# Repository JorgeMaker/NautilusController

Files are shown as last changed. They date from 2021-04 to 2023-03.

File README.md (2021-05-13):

<p align="center">
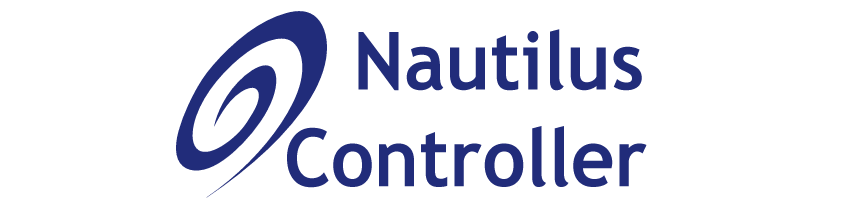
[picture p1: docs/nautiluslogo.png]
  
</p>

## *Nautilus Brushless Controller*

The Nautilus Controller, a project still under development will to turn a hobby brushless motors into a robotic servo actuator  for precise control of 3-phase brushless motors.

The board  integrates the necessary drive electronics, a high performance SMT32 microcontroller, an absolute magnetic encoder, and a high-speed data interface in a compact board that cab be attached at the rear part of a BLDC motor.

<p align="center">
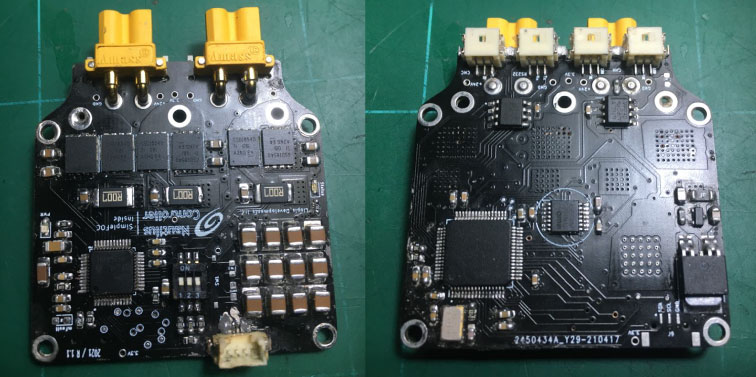
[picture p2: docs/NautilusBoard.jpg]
  
</p>

Some features of the project under development are:

- Compact size of 48x48 mm 4-layer PCB
- SMT32F405RGT6 as MCU
- Uses the DRV8305 as gate driver.
- Absolute 14 bits magnetic encoder AS5048A with SPI communications
- Power Connector: 2x XT30PW-F
- Dual connector of CAN bus interface
- Data Connector: 4x Hirose DF13
- Status LEDs
- RS232 communications
- Temperature sensor

It will be able to operate in in torque, velocity or position modes, using Field Oriented Control (FOC) developed using the open source project [SimpleFOC](https://github.com/simplefoc). For communications it will offer a dual interface based on CAN bus (not implemented yet) for a reliable network communication and RS322 for configuration and basic operation.

The ultimate goal of the controller under development is to be able to develop A ROS actuator that can be used to build dynamic robots like, as for examples, a robot arm or a quadruped robot.

As previously stated, this project is still in the very early stages of development, under construction and continuous change so take it in consideration if you decide to reuse some of the provided information.

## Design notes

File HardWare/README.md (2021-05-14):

### Nautilus Controller Hardware

In this folder you can find the schematic in pdf format to reproduce in your desired EDA software tool. Gerber files are provided too in order to guide you how to layout the components. Since we are in a middle of a global semiconductors shortage BOM is not provided since most probably some of the components used will not be available ;(

<p align="center">
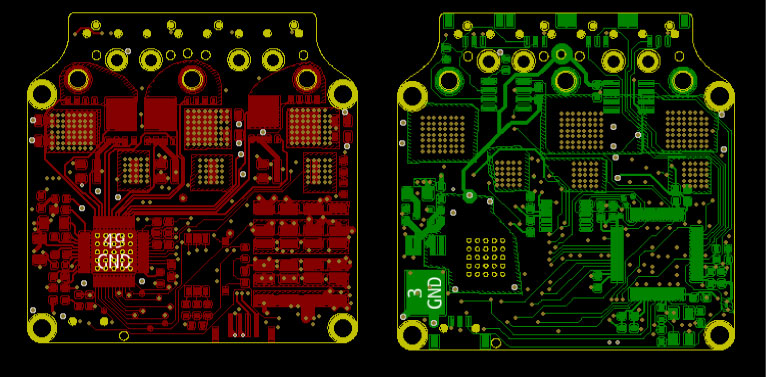
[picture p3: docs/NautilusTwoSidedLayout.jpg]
  
</p>

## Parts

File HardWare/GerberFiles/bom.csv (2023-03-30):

Designator | Footprint | Quantity | Value | LCSC Part #
C1 | 0603 | 1 | 100nF
C10 | 0603 | 1 | 2.2µF
C11 | 0603 | 1 | 15pF
C12 | 0603 | 1 | 15pF
C13 | 1206 | 1 | 4.7μF
C14 | 0603 | 1 | 1µF
C15 | 0603 | 1 | 1µF
C16 | 0603 | 1 | 47nF
C17 | 0603 | 1 | 47nF
C18 | 1206 | 1 | 2.2µF
C19 | 0603 | 1 | 1µF
C2 | 0603 | 1 | 100nF
C20 | 0603 | 1 | 10µF
C21 | 0603 | 1 | 10µF
C22 | 0603 | 1 | 100nF
C23 | 0603 | 1 | 1µF
C24 | 0603 | 1 | 100nF
C25 | 0603 | 1 | 100nF
C26 | 0603 | 1 | 10µF
C27 | 0603 | 1 | 1nF
C28 | 0603 | 1 | 1nF
C29 | 0603 | 1 | 1nF
C3 | 0603 | 1 | 100nF
C30 | 0805 | 1 | 1µF
C31 | 0805 | 1 | 1µF
C32 | 0805 | 1 | 1µF
C33 | 0805 | 1 | 10µF
C34 | 0805 | 1 | 10µF
C35 | 0805 | 1 | 10µF
C36 | 0805 | 1 | 10µF
C37 | 0805 | 1 | 10µF
C38 | 0805 | 1 | 10µF
C39 | 1210 | 1 | 10µF
C4 | 0603 | 1 | 100nF
C40 | 1210 | 1 | 10µF
C41 | 1210 | 1 | 10µF
C42 | 1210 | 1 | 10µF
C43 | 1210 | 1 | 10µF
C44 | 1210 | 1 | 10µF
C45 | 1210 | 1 | 10µF
C46 | 1210 | 1 | 10µF
C47 | 1210 | 1 | 10µF
C48 | 1210 | 1 | 10µF
C49 | 1210 | 1 | 10µF
C5 | 0603 | 1 | 100nF
C50 | 1210 | 1 | 10µF
C51 | 0603 | 1 | 100nF
C52 | 0603 | 1 | 100nF
C6 | 0603 | 1 | 100nF
C7 | 0603 | 1 | 1µF
C8 | 0603 | 1 | 4.7µF
C9 | 0603 | 1 | 2.2µF
D1 | 0603 | 1 | Red
D2 | 0603 | 1 | Green
D3 | 0603 | 1 | Blue
D4 | LED_WS2812B-2020_PLCC4_2.0x2.0mm | 1 | WS2812B
F1 | 1206 | 1 | 500mA | C841189
FB1 | 0603 | 1 | 330Ω @ 100MHz | C35327
H1 | MountingHole_2.5mm_Pad | 1 | H1
H2 | MountingHole_2.5mm_Pad | 1 | H2
H3 | MountingHole_2.5mm_Pad | 1 | H3
H4 | MountingHole_2.5mm_Pad | 1 | H4
HSE1 | TAXM8M4RDBCCT2T | 1 | 8Mhz | C400090
J1 | XT30PW-M | 1 | Power Conn A
J10, J20 | PowerPad | 2 | Rx
J11 | PowerPad | 1 | H
J12 | PowerPad | 1 | SCL
J13, J21 | PowerPad | 2 | Tx
J14 | PowerPad | 1 | L
J15, J9 | PowerPad | 2 | SDA
J16 | JST1.25_3PH | 1 | Comm Conn A
J17 | JST1.25_3PH | 1 | RS232 Conn
J18 | JST1.25_3PH | 1 | Conn Comn B
J19 | PowerPad | 1 | CRTL
J2 | PowerPad | 1 | DIR PAD
J3 | PowerPad | 1 | STEP PAD
J4 | XT30PW-M | 1 | Power Conn B
J5 | SolderRescue | 1 | LOOP PIN
J6 | PinHeader_1x04_P2.00mm_Vertical | 1 | Prog conn
J7 | SolderRescue | 1 | CAN_RX
J8 | SolderRescue | 1 | CAN_TX
Q1 | SSOT-3 | 1 | FDN352AP
Q2, Q3, Q4, Q5, Q6, Q7 | BSC022N04LS6ATMA1 | 6 | BSC022N04LS
R1 | 0603 | 1 | 1KΩ
R10 | 0603 | 1 | 10KΩ
R11, R12, R13 | CurrentSense | 3 | 2mΩ
R14 | 0603 | 1 | 10KΩ
R15 | 0603 | 1 | 120Ω
R16 | 0603 | 1 | 10KΩ
R2 | 0603 | 1 | 10KΩ
R3 | 0603 | 1 | 10K
R4 | 0603 | 1 | 220Ω
R5 | 0603 | 1 | 100Ω
R6 | 0603 | 1 | 10KΩ
R7 | 0603 | 1 | 20KΩ
R8 | 0603 | 1 | 2KΩ
R9 | 0603 | 1 | 10KΩ
SW1 | SimplePushButton | 1 | Reset Push
TP1 | MinimalTP | 1 | INH_A_TP
TP10, TP11 | MinimalTP | 2 | INL_C_TP
TP12 | MinimalTP | 1 | mFAULT
TP13 | MinimalTP | 1 | MOSI_ENC
TP14 | MinimalTP | 1 | MISO_ENC
TP15 | MinimalTP | 1 | CLK_ENC
TP16 | MinimalTP | 1 | CS_ENC
TP17 | MinimalTP | 1 | ENC PWM
TP18 | MinimalTP | 1 | SENSE A
TP19 | MinimalTP | 1 | SENSE C
TP2 | MinimalTP | 1 | CS
TP20 | MinimalTP | 1 | SENSE B
TP3 | MinimalTP | 1 | INL_A_TP
TP4 | MinimalTP | 1 | MOSI
TP5 | MinimalTP | 1 | INH_B_TP
TP6 | MinimalTP | 1 | MISO
TP7 | MinimalTP | 1 | INL_B_TP
TP8 | MinimalTP | 1 | CLK
TP9 | MinimalTP | 1 | INH_C_TP
U1 | TO114P998X235-5 | 1 | BD33C0AWFP
U10, U12, U8, U9 | PowerPad | 4 | Power24VPad
U11 | PowerPad | 1 | PowerPad I2C
U13 | MinimalPhasePad | 1 | PhaseA
U14 | MinimalPhasePad | 1 | PhaseB
U15 | MinimalPhasePad | 1 | PhaseC
U2 | LQFP-64_10x10mm_P0.5mm | 1 | STM32F405RGT6
U3 | QFP50P900X900X120-49N | 1 | DRV8305 | LCSC Part #
U4 | SOP-8_3.9x4.9mm_P1.27mm | 1 | LM75B
U5 | SOIC-8_3.9x4.9mm_P1.27mm | 1 | SN65HVD231 | C12084
U6 | TSSOP-14_4.4x5mm_P0.65mm | 1 | AS5048A | C2655181
U7 | MiniLogo | 1 | Logo

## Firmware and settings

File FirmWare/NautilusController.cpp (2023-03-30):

#include <SimpleFOC.h>
#include "STM32F405RTGBorad.h"
#include <SimpleCanFacility.h>
#include <NautilusCANMessage.h>
#include <TrapezoidalPlanner.h>
#include <Adafruit_NeoPixel.h>
#include <TemperatureSensor.h>

///    SPI 2 (AS5048A)
#define MOSI_DRV  PA7  // Blue
#define MISO_DRV  PA6 // Green
#define CLK_DRV   PA5 // Orange
#define CS_DRV    PA4  // Yellow

///     SPI 1  (DRV8305)
#define MOSI_ENC PB15 // Blue
#define MISO_ENC PB14  // Green
#define CLK_ENC  PB13   // Orange
#define CS_ENC   PB12    // Yellow

#define INH_A PC7 // TIM8_CH2
#define INH_B PA1 // TIM2_CH2
#define INH_C PA3 // TIM2_CH4

#define INL_A PC6 // TIM8-CH1
#define INL_B PA0 // TIM2-CH1
#define INL_C PA2 // TIM2-CH3

#define ENA_GATE PC3

#define SENSE_A PB1
#define SENSE_B PB0
#define SENSE_C PC5

#define BLUE_LED PB2
#define LOOP_PIN PC13

#define RGB_PIN PB5
#define LED_COUNT  1

#define NUM_OF_BLINKS 16

void bootLedIndicator()
{
  int counter = NUM_OF_BLINKS;
  pinMode(BLUE_LED, OUTPUT);
  while (counter > 0)
  {
    digitalToggle(BLUE_LED);
    delay(50);
    counter--;
  }
}

Adafruit_NeoPixel regIndicator = Adafruit_NeoPixel(LED_COUNT, RGB_PIN, NEO_GRB + NEO_KHZ800);
bool regIndicatorStatus = false;

void initRGBIndicator(){
    regIndicator.begin();
    regIndicator.setBrightness(20);
} 
void showRGBColor(int red, int green, int blue){
    regIndicator.setPixelColor(0, regIndicator.Color(red, green, blue));
    regIndicatorStatus = true;
    regIndicator.show();
}

void setRGBColor(int red, int green, int blue){
    regIndicator.setPixelColor(0, regIndicator.Color(red, green, blue));
}

 void togggleRGB(){
    if (regIndicatorStatus){
      regIndicator.setBrightness(0);
      regIndicator.show();
    }
    else{
      regIndicator.setBrightness(15);
      regIndicator.setPixelColor(0, regIndicator.Color(255, 0, 255));
      regIndicator.show();
    }
    regIndicatorStatus = !regIndicatorStatus;
 }



SimpleCanFacility canFacility;
NautilusCANMesage nautilusMsg;
double lastTime;

SPIClass spiConnectionDRV(MOSI_DRV, MISO_DRV, CLK_DRV);

void configureAmplierClamping(SPIClass spiConnectionToDRV){
  // Clamp sense amplifier output to 3.3V
  digitalWrite(CS_DRV, LOW);
  byte resp1 = spiConnectionToDRV.transfer(B01001100);
  byte resp2 = spiConnectionToDRV.transfer(B10100000);
  digitalWrite(CS_DRV, HIGH);
  Serial.println("Configure Amplier Clamping");
  Serial.print("Byte 0 : ");
  Serial.println(resp1, BIN);
  Serial.print("Byte 1 : ");
  Serial.println(resp2, BIN);
}
void configure6PWM_Mode(SPIClass spiConnectionToDRV){
  // Set to three PWM inputs mode to 6PWM
  digitalWrite(CS_DRV, LOW);
  byte resp1 = spiConnectionToDRV.transfer(B00111010);
  byte resp2 = spiConnectionToDRV.transfer(B0000110);
  digitalWrite(CS_DRV, HIGH);
  Serial.println("Configure 6PWM Mode");
  Serial.print("Byte 0 : ");
  Serial.println(resp1, BIN);
  Serial.print("Byte 1 : ");
  Serial.println(resp2, BIN);
}

void drv8305Initialization()
{
  Serial.println("DRIVER: DRV8305 INIT");
  pinMode(ENA_GATE, OUTPUT);
  pinMode(CS_DRV, OUTPUT);
  digitalWrite(CS_DRV, HIGH);
  configure6PWM_Mode(spiConnectionDRV);
  configureAmplierClamping(spiConnectionDRV);
  _delay(500);
  Serial.println("DRIVER: enGate Enabled");
  digitalWrite(ENA_GATE, HIGH);
}

MagneticSensorSPIConfig_s AS5047A_SPI_Config{
    .spi_mode = SPI_MODE1,
    .clock_speed = 10000000,
    .bit_resolution = 14,
    .angle_register = 0x3FFF,
    .data_start_bit = 13,
    .command_rw_bit = 14,
    .command_parity_bit = 15};

MagneticSensorSPI sensor = MagneticSensorSPI(AS5047A_SPI_Config, CS_ENC);

SPIClass spiConnectionEncoder(MOSI_ENC, MISO_ENC, CLK_ENC);

// BLDC motor & driver instance
BLDCMotor motor = BLDCMotor(7);
//BLDCMotor motor = BLDCMotor(12);

// BLDCDriver3PWM driver = BLDCDriver3PWM (INH_A,INH_B, INH_C, ENA_GATE);
BLDCDriver6PWM driver = BLDCDriver6PWM(INH_A, INL_A, INH_B, INL_B, INH_C, INL_C, ENA_GATE);

LowsideCurrentSense current_sense = LowsideCurrentSense(0.007f, 12.22f, SENSE_A, SENSE_B, SENSE_C);

Commander commander = Commander(Serial);

TrapezoidalPlanner planner(10);

TemperatureSensor temperature;

void doPlanner(char *cmd){
  planner.doTrapezoidalPlannerCommand(cmd);
}

void doMotor(char *cmd){
  commander.motor(&motor, cmd);
}

void configureNuathilus(){
  // control loop type and torque mode
  motor.torque_controller = TorqueControlType::foc_current;
  motor.controller = MotionControlType::velocity_openloop;
  motor.motion_downsample = 0.0;
  driver.voltage_power_supply = 22;
  
  // velocity loop PID
  motor.PID_velocity.P = 10.0;
  motor.PID_velocity.I = 10.0;
  motor.PID_velocity.D = 0.0;
  motor.PID_velocity.output_ramp = 1000.0;
  motor.PID_velocity.limit = 20.0;
  // Low pass filtering time constant
  motor.LPF_velocity.Tf = 0.2;
  
  // angle loop PID
  motor.P_angle.P = 10.0;
  motor.P_angle.I = 1.0;
  motor.P_angle.D = 0.0;
  motor.P_angle.output_ramp = 0.0;
  motor.P_angle.limit = 10.0;
  // Low pass filtering time constant
  motor.LPF_angle.Tf = 0.3;
  
  // current q loop PID
  motor.PID_current_q.P = 3.0;
  motor.PID_current_q.I = 300.0;
  motor.PID_current_q.D = 0.0;
  motor.PID_current_q.output_ramp = 0.0;
  motor.PID_current_q.limit = 12.0;
  
  // Low pass filtering time constant
  motor.LPF_current_q.Tf = 0.005;
  
  // current d loop PID
  motor.PID_current_d.P = 3.0;
  motor.PID_current_d.I = 300.0;
  motor.PID_current_d.D = 0.0;
  motor.PID_current_d.output_ramp = 0.0;
  motor.PID_current_d.limit = 12.0;
  
  // Low pass filtering time constant
  motor.LPF_current_d.Tf = 0.005;
  
  
  // Limits
  motor.velocity_limit = 30.0;
  motor.voltage_limit = 1;

  // motor.current_limit = 2.0;

  //  general settings
  //  pwm modulation settings
  motor.foc_modulation = FOCModulationType::SinePWM;
  motor.modulation_centered = 1.0;
}

void setup(){

  bootLedIndicator();
  Serial.begin(115200);

  initRGBIndicator();
  setRGBColor(255,0,0);

  // I2C for temperature Sensor
  Wire.begin(PB7, PB6);

  Serial.println("Starting Motor configuration ....");

  canFacility.init(Kbit250, NormalCAN);
  canFacility.configSnniferFilter();
  canFacility.activateNotification();
  canFacility.begin();

  lastTime = millis();

  pinMode(LOOP_PIN, OUTPUT);

  char motor_id = 'M';
  commander.add(motor_id, doMotor, "Motor");

  motor.useMonitoring(Serial);
  pinMode(BLUE_LED, OUTPUT);
  sensor.init(&spiConnectionEncoder);

  // DRV8305 Inicialization
  spiConnectionDRV.begin();
  spiConnectionDRV.setBitOrder(MSBFIRST);
  spiConnectionDRV.setDataMode(SPI_MODE1);
  spiConnectionDRV.setClockDivider(SPI_CLOCK_DIV8);
  drv8305Initialization();


  // Configure and init Temperature Sensor
  temperature.init();

  ///   TODO TODO TODO
  ///   RESOLVE HW ISSUE
  // link the motor to the sensor
  //motor.linkSensor(&sensor);

  driver.voltage_power_supply = 22;
  driver.init();
  driver.enable();

  // link the motor and the driver
  motor.linkDriver(&driver);
  configureNuathilus();

  //  GCode move Gxx, GVxx, or GAxx - Example: G30 moves to position in rads. 
  //  GV10 sets velocity to 10 rads/s. GA5 sets acceleration to 5 rads/s/s.");
  planner.linkMotor(&motor);
  commander.add('G', doPlanner, "Motion Planner");

  motor.target = 10;
 
  Serial.println("LCS ready to be linked ...");
  current_sense.linkDriver(&driver);
  Serial.println("LCS ready just linked ...");
  current_sense.init();
  Serial.println("LCS ininitiated ...");
  // link the current sense to the motor
  motor.linkCurrentSense(&current_sense);
  Serial.println("LCS lined with motor ...");
  // skip alignment
  current_sense.skip_align = true;
  //current_sense.driverAlign();

  // initialize motor
  motor.init();
  motor.initFOC();

  Serial.println("Motor ready.");
  _delay(1000);
}

float value;

void sendTemperatureByCanBus(){
  nautilusMsg.setEncodeMessageID(ANGLE_STATE, FLOAT, 5, 0, 10);
  float temp = temperature.readTemperatureC();
  nautilusMsg.setFloatPayload(temp);
  canFacility.send(nautilusMsg.toCanMessage());
}

CanMessage rxMsgBuff[3];
int nodeID = 5;
int entity = 10;

void attendCanBusCommands(){
  int receivedMessages = canFacility.receiveCanMessages(rxMsgBuff);
  if (receivedMessages > 0){
    togggleRGB();
    //digitalToggle(BLUE_LED);
    for (int index = 0; index < receivedMessages; index++){
      NautilusCANMesage nautilusMsg = rxMsgBuff[index];
      if ((nautilusMsg.getNodeID() == nodeID) & (nautilusMsg.getEntity() == entity)){
        if (nautilusMsg.getCommandID() == TARGET_CMD){
          motor.target = nautilusMsg.getFloatPayload();
          motor.move(motor.target);
        }
      }
    }
  }
}

void loop()
{

  if ((millis() - lastTime) > 100){
    digitalToggle(BLUE_LED);
    sendTemperatureByCanBus();
    lastTime = millis();
  }
  
  motor.loopFOC();
  motor.move();
  commander.run();
  planner.runPlannerOnTick();
  motor.monitor();
  attendCanBusCommands();
  
  digitalToggle(LOOP_PIN);
}

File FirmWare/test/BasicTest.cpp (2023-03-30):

/*
#include <SimpleFOC.h>
#include "STM32F405RTGBorad.h"

///    SPI 2 (AS5048A)
#define MOSI_DRV PA7 // Blue
#define MISO_DRV PA6 // Green
#define CLK_DRV PA5  // Orange
#define CS_DRV PA4   // Yellow

///     SPI 1  (DRV8305)
#define MOSI_ENC PB15 // Blue
#define MISO_ENC PB14 // Green
#define CLK_ENC PB13  // Orange
#define CS_ENC PB12   // Yellow

#define INH_A PC7 // TIM8_CH2
#define INH_B PA1 // TIM2_CH2
#define INH_C PA3 // TIM2_CH4

#define INL_A PC6 // TIM8-CH1
#define INL_B PA0 // TIM2-CH1
#define INL_C PA2 // TIM2-CH3

#define ENA_GATE PC3
#define nMFAULT PC4  

#define BLUE_LED PB2
#define LOOP_PIN PC13

#define BLUE_LED PB2
#define LOOP_PIN PC13

#define SENSE_A PB1
#define SENSE_B PB0
#define SENSE_C PC5


#define NUM_OF_BLINKS 15

void bootLedIndicator()
{
  int counter = NUM_OF_BLINKS;
  pinMode(BLUE_LED, OUTPUT);
  while (counter > 0)
  {
    digitalToggle(BLUE_LED);
    delay(50);
    counter--;
  }
}
double lastTime;

void setOutPutMode(){

  pinMode(MOSI_DRV, OUTPUT);
  pinMode(MISO_DRV, OUTPUT);
  pinMode(CLK_DRV, OUTPUT);
  pinMode(CS_DRV, OUTPUT);

  pinMode(MOSI_ENC, OUTPUT);
  pinMode(MISO_ENC, OUTPUT);
  pinMode(CLK_ENC, OUTPUT);
  pinMode(CS_ENC, OUTPUT);

  pinMode(INH_A, OUTPUT);
  pinMode(INH_B, OUTPUT);
  pinMode(INH_C, OUTPUT);

  pinMode(INL_A, OUTPUT);
  pinMode(INL_B, OUTPUT);
  pinMode(INL_C, OUTPUT);

  pinMode(ENA_GATE, OUTPUT);
  pinMode(nMFAULT, OUTPUT);

  pinMode(SENSE_A, OUTPUT);
  pinMode(SENSE_B, OUTPUT);
  pinMode(SENSE_C, OUTPUT);

}

void togglePins(){
  digitalToggle(MOSI_DRV);
  digitalToggle(MISO_DRV);
  digitalToggle(CLK_DRV);
  digitalToggle(CS_DRV);

  digitalToggle(MOSI_ENC);
  digitalToggle(MISO_ENC);
  digitalToggle(CLK_ENC);
  digitalToggle(CS_ENC);

  digitalToggle(INH_A);
  digitalToggle(INH_B);
  digitalToggle(INH_C);

  digitalToggle(INL_A);
  digitalToggle(INL_B);
  digitalToggle(INL_C);

  digitalToggle(ENA_GATE);
  digitalToggle(nMFAULT);

  digitalToggle(SENSE_A);
  digitalToggle(SENSE_B);
  digitalToggle(SENSE_C);

}

void setup()
{
  Serial.begin(115200);
  pinMode(BLUE_LED, OUTPUT);
  pinMode(LOOP_PIN, OUTPUT);

  setOutPutMode();
  bootLedIndicator();
  lastTime = millis();
}

void loop()
{

  if ((millis() - lastTime) > 100){
    Serial.println("Hola Nautilus !!");
    digitalToggle(BLUE_LED);
    lastTime = millis();
  }
  togglePins();
  digitalToggle(LOOP_PIN);
  delay(1);
}
*/

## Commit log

2021-05-13 Added schematic and gerber files
    [Nauthiluscontroller-B_Cu.gbr, Nauthiluscontroller-B_Mask.gbr, Nauthiluscontroller-B_Paste.gbr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]
2023-03-30 Updated HW info for V3.0
    Schematics and Gerber files updated
    [Nauthiluscontroller-B_Cu.gbr, Nauthiluscontroller-B_Mask.gbr, Nauthiluscontroller-B_Paste.gbr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]
2023-03-30 Updated FirmWare files
    Updated FW for the new HW and added new functionalities: CanBusFacility, NautilusCanBUSMessage , etc
2023-03-30 Update STM32F405RTGBorad.h
    Cleanup of commented lines
2023-03-30 Solved SENSE_C issue
    Modification to solve SENSE_C at LowsideCurrentSense
    [NautilusController.cpp]
